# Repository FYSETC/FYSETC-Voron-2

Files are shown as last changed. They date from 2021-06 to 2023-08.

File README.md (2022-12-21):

# FYSETC-VORON-2.4

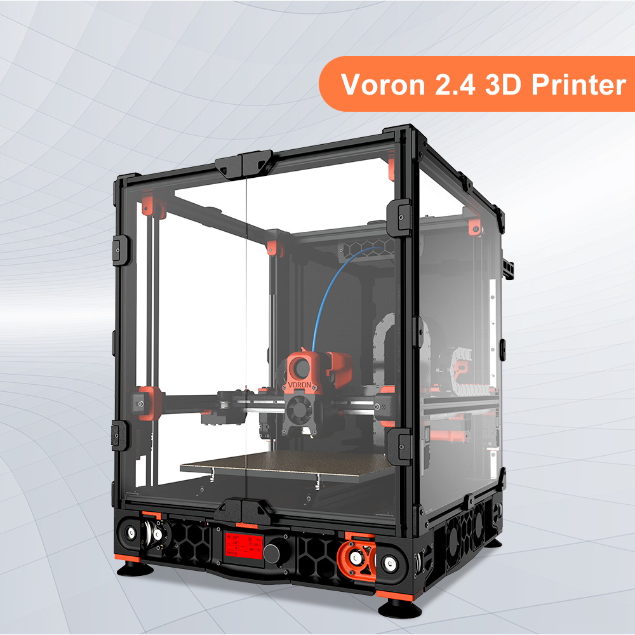
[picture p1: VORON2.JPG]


## 1. Project

This is FYSETC's project database for VORON 2.4 kit, which is convenient for you to find information. Thanks for VORON Team's great work, they always design fantastic printers.

Official website:：https://vorondesign.com/voron2.4
Official Github：https://github.com/VoronDesign/Voron-2/tree/V2.4r2

In folder `Voron-2-Voron2.4` beside this README file, we make some small changes base on the VORON official material. Like change the board to Spider and others. 

## 2. BOM & Changes

Please check BOM [here](https://github.com/FYSETC/FYSETC-Voron-2/blob/main/BOM.md).

### VORON 2.4 R2

## 3. Extra parts

Besides the parts in Voron sourcing guide, we offer extra useful parts for you.

### Wire connector

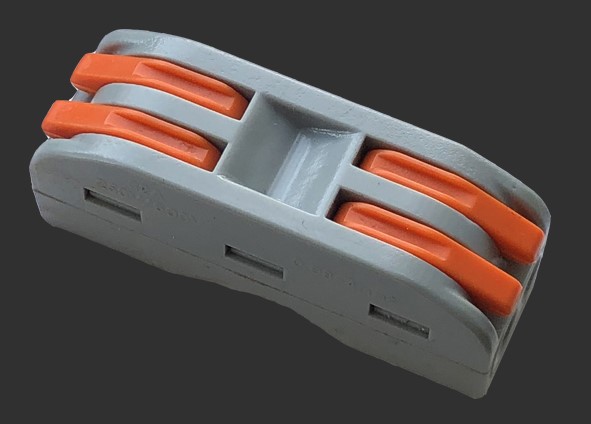
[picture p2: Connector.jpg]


This is for fans wire connection, with this connector you can wire two or more fans to one side of the connector, and the other side  to Spider board. Then you can control the two or more fans with one control pin in Spider.

## 4. Printed parts:

You can find all printed parts in VORON [website](https://vorondesign.com/voron2.4), VORON [github](https://github.com/VoronDesign/Voron-2).

Printed parts are not included in our VORON 2.4 kit. As VORON official provide you options on some particular printed part of the machine. Like the plug panel at the back of VORON machine, you can choose [plug_panel](https://github.com/VoronDesign/Voron-2/blob/Voron2.4/STLs/VORON2.4/Electronics_Compartment/Plug_Panel/plug_panel.stl) or [plug_panel_filtered_mains](https://github.com/VoronDesign/Voron-2/blob/Voron2.4/STLs/VORON2.4/Electronics_Compartment/Plug_Panel/plug_panel_filtered_mains.stl). So in our kit, we also need to choose too, below is our choice.

| Revision 1.0 | Revision 1.1 | Revision 1.2 | Revision 1.3 | R2 |
| --- | --- | --- | --- | --- |
| [plug panel](https://github.com/VoronDesign/Voron-2/blob/Voron2.4/STLs/VORON2.4/Electronics_Compartment/Plug_Panel/plug_panel.stl), [Microswitch edge pod](https://github.com/VoronDesign/VoronUsers/blob/master/printer_mods/randell/Microswitch_Endstop/Microswitch_Edge_Pod.stl), [Z Chain mount part 1](https://github.com/FYSETC/FYSETC-Voron-2/blob/main/Z_Chain_Lower_Mount.STL), [Z Chain mount part 2](https://github.com/FYSETC/FYSETC-Voron-2/blob/main/Z_Chain_Upper_Mount.STL), Spider board mount | [plug panel](https://github.com/VoronDesign/Voron-2/blob/Voron2.4/STLs/VORON2.4/Electronics_Compartment/Plug_Panel/plug_panel.stl), [Microswitch edge pod](https://github.com/VoronDesign/VoronUsers/blob/master/printer_mods/randell/Microswitch_Endstop/Microswitch_Edge_Pod.stl), [Z Chain mount part 1](https://github.com/FYSETC/FYSETC-Voron-2/blob/main/Z_Chain_Lower_Mount.STL), [Z Chain mount part 2](https://github.com/FYSETC/FYSETC-Voron-2/blob/main/Z_Chain_Upper_Mount.STL), Spider board mount | [plug panel](https://github.com/VoronDesign/Voron-2/blob/Voron2.4/STLs/VORON2.4/Electronics_Compartment/Plug_Panel/plug_panel.stl), [Microswitch edge pod](https://github.com/VoronDesign/VoronUsers/blob/master/printer_mods/randell/Microswitch_Endstop/Microswitch_Edge_Pod.stl), [Z Chain mount part](https://github.com/VoronDesign/VoronUsers/tree/master/printer_mods/KiloQubit/VORON_2.4_Z_Chain_3_Hole_Mounts), Spider board mount | [plug panel](https://github.com/VoronDesign/Voron-2/blob/Voron2.4/STLs/VORON2.4/Electronics_Compartment/Plug_Panel/plug_panel.stl), [Microswitch edge pod](https://github.com/VoronDesign/VoronUsers/blob/master/printer_mods/randell/Microswitch_Endstop/Microswitch_Edge_Pod.stl), [Z Chain mount part](https://github.com/VoronDesign/VoronUsers/tree/master/printer_mods/KiloQubit/VORON_2.4_Z_Chain_3_Hole_Mounts), Spider board mount | [Microswitch_Z_Endstop_new_shorter](https://github.com/VoronDesign/Voron-Hardware/tree/master/Microswitch_Z_Endstop/STLs) |

## 5. Wiring

### 5.1 Spider 1.x wiring

There is wiring from VORON community [here](https://github.com/shiftingtech/Voron-Documentation/blob/Spider/build/electrical/v2_spider_wiring.md). Also you can refer Spider wiring [here](https://github.com/FYSETC/FYSETC-SPIDER#3-hardware-guide).

***Note: Check your fan voltage before you set the fan jumpers, the jumpers for fan in below diagram are all set to 24v.***

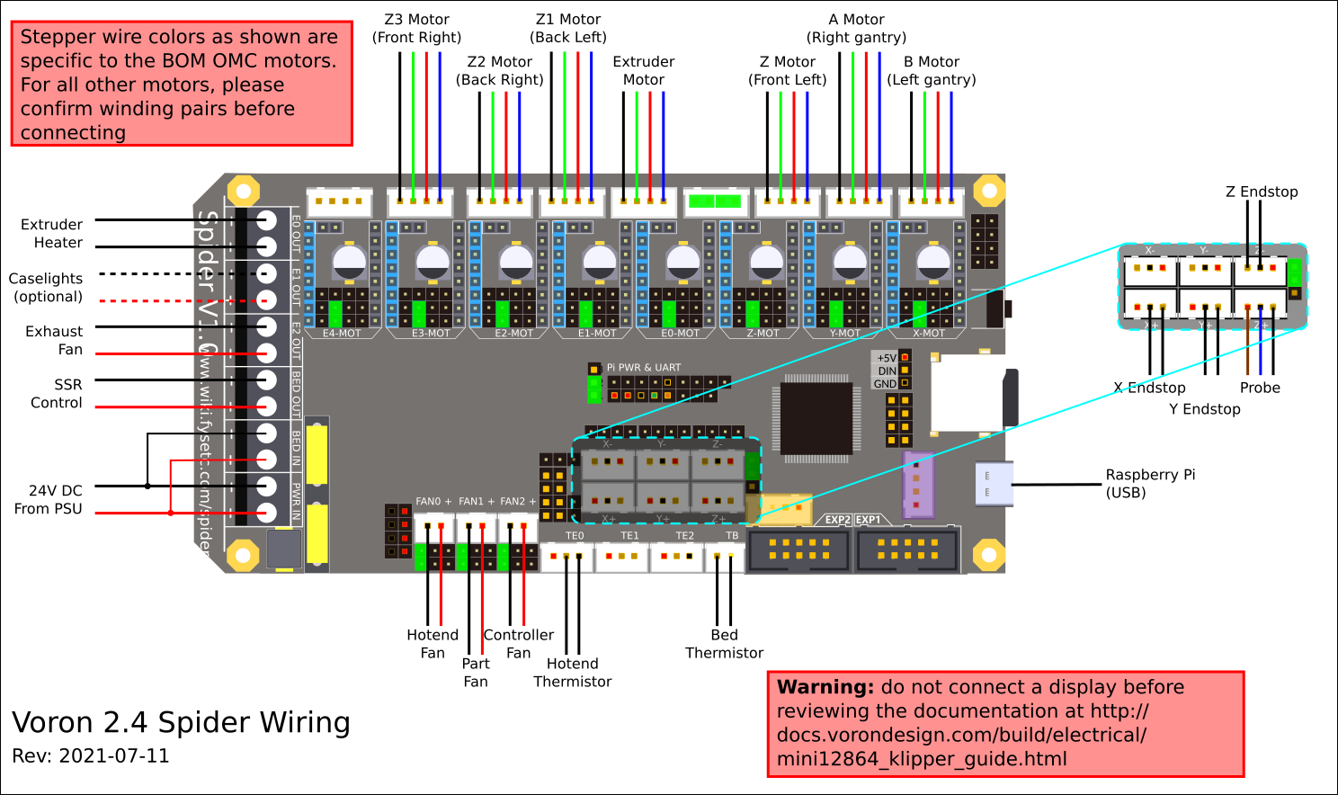
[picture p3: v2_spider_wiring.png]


### 5.2 Spider v2.2 wiring

#### 5.2.1 VORON 2.4 kit wiring

If the pic is not clear enough, please check PDF file [here](https://github.com/FYSETC/FYSETC-Voron-2/blob/main/VORON2.4_SPIDER_V22_WIRING.pdf).



#### 5.2.2 VORON 2.4 R2 kit wiring

##### Spider 2.2

If the pic is not clear enough, please check PDF file [here](https://github.com/FYSETC/FYSETC-Voron-2/blob/main/VORON2.4R2_SPIDER_V22_Wiring_S.pdf).

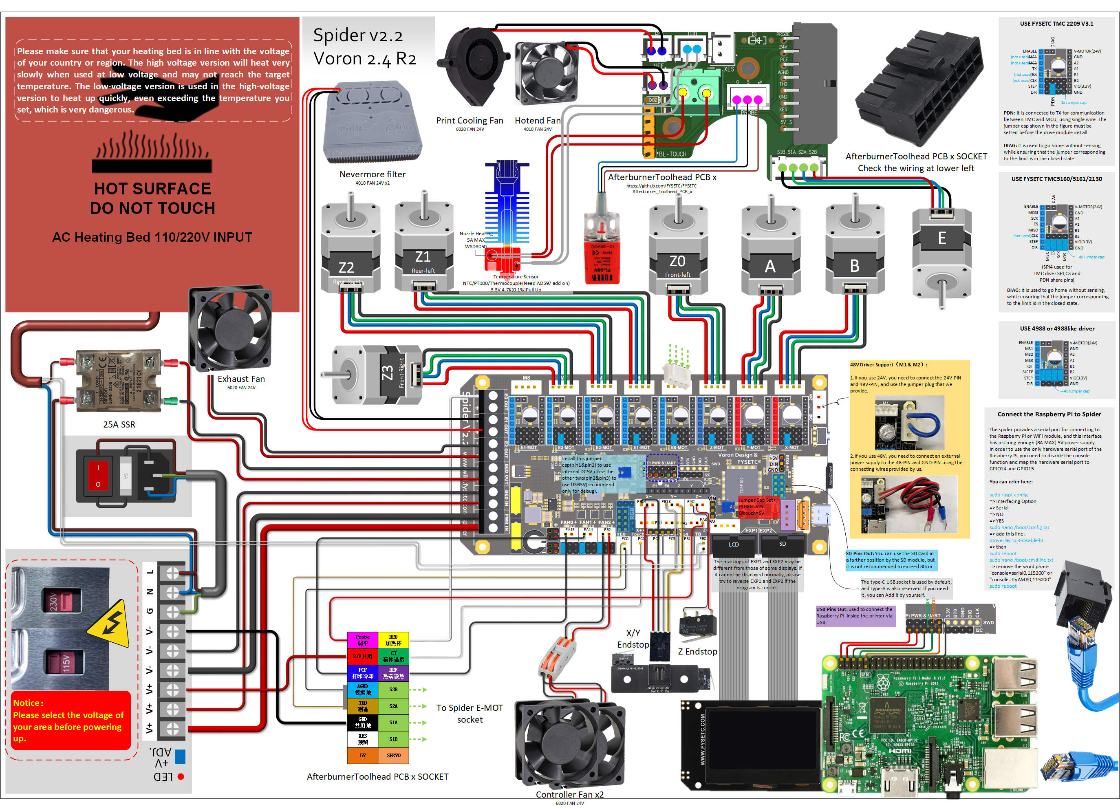
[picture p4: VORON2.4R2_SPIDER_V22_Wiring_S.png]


If the pic is not clear enough, please check PDF type [here](https://github.com/FYSETC/FYSETC-Voron-2/blob/main/VORON2.4R2_SPIDER_V22_Wiring.pdf).

##### Spider 2.3

If the pic is not clear enough, please check PDF file [here](https://github.com/FYSETC/FYSETC-Voron-2/blob/main/VORON2.4R2_SPIDER_V23_Wiring_S.pdf).

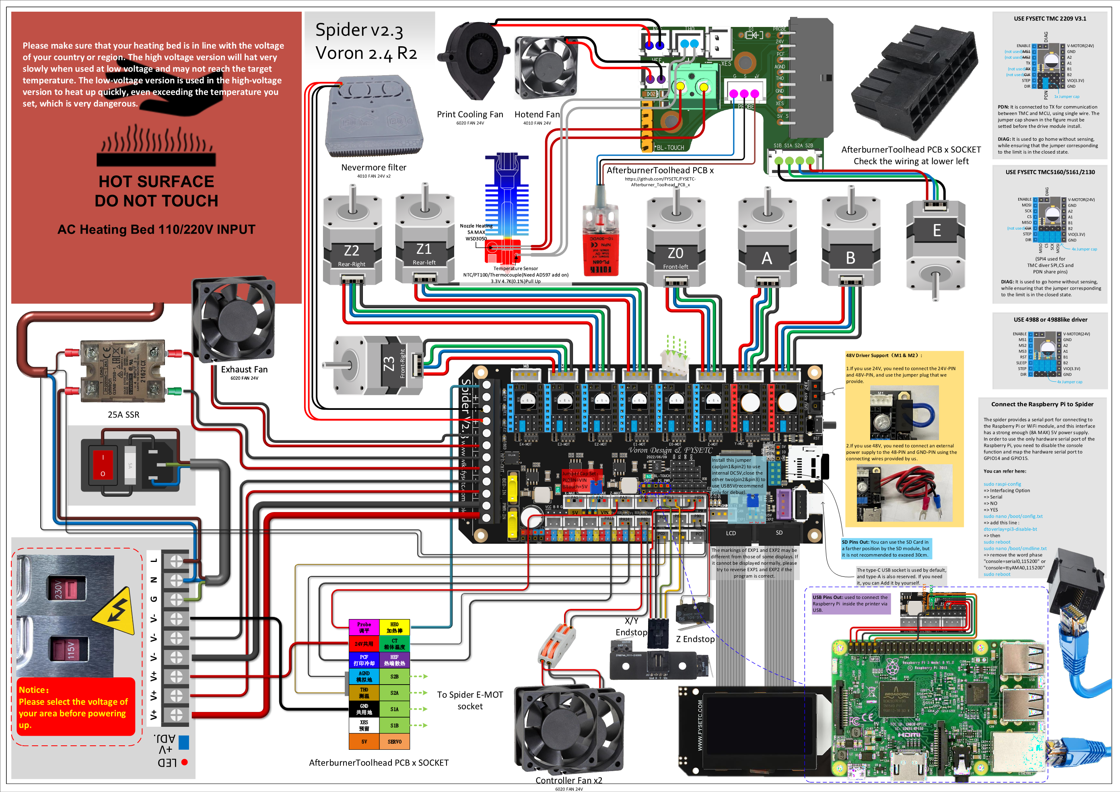
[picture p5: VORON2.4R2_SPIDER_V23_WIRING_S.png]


If the pic is not clear enough, please check PDF type [here](https://github.com/FYSETC/FYSETC-Voron-2/blob/main/VORON2.4R2_SPIDER_V23_Wiring.pdf).



### 5.3 XY endstop

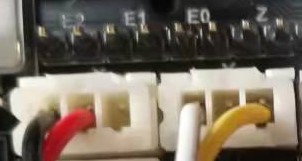
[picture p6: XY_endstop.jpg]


## 6. Firmware&OS

You can find example Klipper printer.cfg file on VORON github [here](https://github.com/VoronDesign/Voron-2/tree/Voron2.4/firmware/klipper_configurations/Spider) or our Spider github [here](https://github.com/FYSETC/FYSETC-SPIDER/blob/main/firmware/Klipper/printer.cfg) or gitee [here](https://gitee.com/fysetc-mirrors/FYSETC-SPIDER/tree/main/firmware/Klipper). And you can get our pre-build firmware and OS image in the `firmware&OS` folder next to this `README` file. 

## 7. Where to buy the kit

[Aliexpress](https://www.aliexpress.com/item/1005002782065110.html)

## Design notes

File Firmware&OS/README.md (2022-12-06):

# Firmware&OS

## 1. Firmware

There is pre-build firmware named `firmware.bin`, please flash it to Spider board flash address `0x08008000`. You can follow Spider firmware upload instruction here ([github](https://github.com/FYSETC/FYSETC-SPIDER#44--firmware-upload) [gitee](https://github.com/FYSETC/FYSETC-SPIDER#44--firmware-upload)).

And the menuconfig of this pre-build firmware is below.

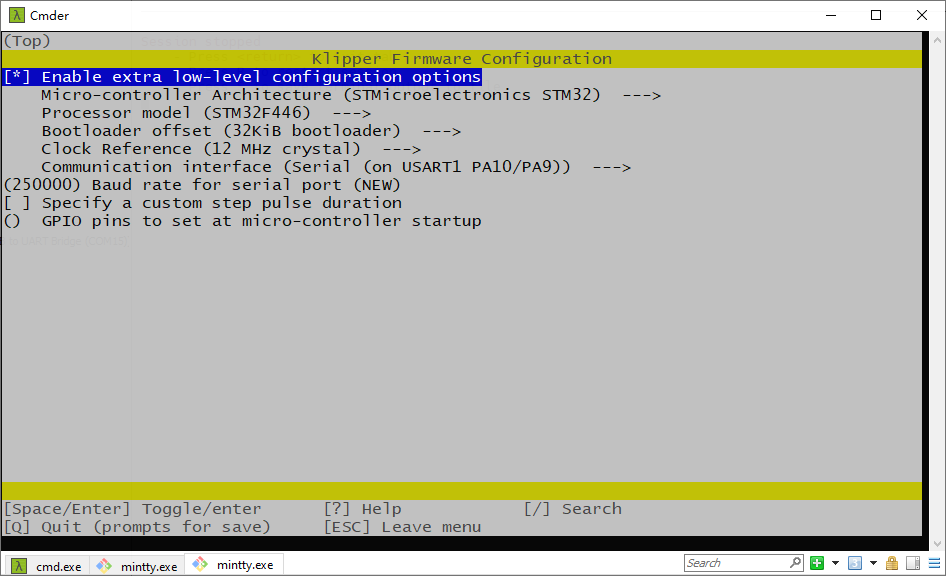
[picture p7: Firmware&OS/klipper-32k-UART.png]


## 2. OS

We provide you two OS images choices: Mainsail OS and Octopi OS.

### 2.1 Mainsail OS

You can get the corresponding Mainsail OS here ([1.Dropbox](https://www.dropbox.com/s/y8eb1giik5p6n1d/VORON2.4R2-Spider2.x-Mainsail.zip?dl=0)).

### 2.2 Octopi OS

If your kit version is rev1.0 or rev1.1, your Spider board version is 1.x, you can get the responding Octopi system here([1.Dropbox](https://www.dropbox.com/s/vtbbxu55y27kbl7/VORON2.4-Octoprint-Klipper.img?dl=0) [2.百度云盘](https://pan.baidu.com/s/1aeOkN2ZxQb99EaApOWNglw) 提取码：1357) . If your kit version is rev1.2, then your Spider board version is 2.2, and you can get the responding Octopi system here([1.Dropbox](https://www.dropbox.com/s/mn1kvcndi1gpb9v/VORON2.4-Spider2.x-Octoprint-Klipper.img?dl=0) [2.百度云盘](https://pan.baidu.com/s/1OZLoSdPNHbxYGWpk1KwKzA) 提取码：YYDS).

You can login in Octoprint with the following account and password.

```
Account: FYSETC
Password: 12345678
```

### 2.3 How to flash OS image

Before flash, you need an SD card , minimum requirement of SD card capacity is 8G. Please prepare that first. And then you can use this software [here](https://www.balena.io/etcher/) to install. Well that are so many OS flash tool that you can use. And there are a lot of tutorial if you google `how to flash os image`.

### 2.4 SSH account and password

OS SSH account and password

```
Account: pi
Password: raspberry
```

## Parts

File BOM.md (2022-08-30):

# Package list 

## Revision 1.0

| Index | Sort | Component | Qty | Note |
| ----- | --- | --- | --- | --- |
| 1 | Fasteners | Voron V2.4 fasteners Pack | 1 SET | |
| 2 | Motion | GT2 Open Belt LL-2GT-6 (6mm wide) - 4000mm | 1 PC | |
| 3 | Motion | GT2 Open Belt LL-2GT-9 (9mm wide) - 4440mm | 1 PC | |
| 4 | Motion | GT2 Belt Loop (6mm W) - 188mm | 4 PCS | |
| 5 | Motion | GT2 20T Pulley (5mm ID 6mm W) | 3 PCS | |
| 6 | Motion | GT2 16T Pulley (5mm ID 6mm W) | 4 PCS | |
| 7 | Motion | GT2 20T Pulley (5mm ID 9mm W) | 4 PCS | |
| 8 | Motion | GT2 20T Toothed Idler (5mm ID 6mm W) | 2 PCS | |
| 9 | Motion | GT2 20T Toothed Idler (5mm ID 9mm W) | 4 PCS | |
| 10 | Motion | GT2 80T Pulley (5mm ID 6mm W) | 4 PCS | |
| 11 | Motion | F695 Bearing | 20 PCS | |
| 12 | Motion | 625 Bearing | 12 PCS | |
| 13 | Motion | 5x60mm Shaft | 4 PCS | |
| 14 | Motion | 5x30mm Shaft | 1 PC | |
| 15 | Motion | Linear Rail MGN9H 400mm | 8 PCS | |
| 16 | Vibration Management | Rubber Compressor Foot | 4 PCS | |
| 17 | Electronics | XY Microswitch Endstop / Z Endstop | 1 PC / 1 SET | [Here](https://github.com/VoronDesign/Voron-Hardware/tree/master/Microswitch_Endstop) |
| 18 | Electronics | PL-08N Inductive Probe | 1 PC | |
| 19 | Electronics | SSR: G3A-210B-DC5 | 1 PC | |
| 20 | Electronics | NEMA17 Motor TB-3544(check [here](https://github.com/FYSETC/FYSETC-MOTORS/tree/main/TB-3544)) | 6 PCS | 5x1m cables for Z0 Z1 Z2 Z3 and B motor, 1x1.4m for A motor  |
| 21 | Electronics | NEMA17 Motor MSM-30010-R0005(check [here](https://github.com/FYSETC/FYSETC-MOTORS/tree/main/MSM-30010-R0005)) | 1 PC | 1x2.3m for E motor |
| 22 | Electronics | Mean Well LRS-200-24 PSU | 1 PC | |
| 23 | Electronics | Inlet Power Socket IEC320 C14 | 1 SET | |
| 24 | Electronics | 40x40x10 Axial Fan (24V) | 1 PCS | |
| 25 | Electronics | 40x40x20 Centrifugal Fan (24V) | 1 PC | |
| 26 | Electronics | 60x60x20 Fan (24V)kit | 1 SET | |
| 27 | Electronics | Keystone CAT6 Insert (Optional) | 1 PC | |
| 28 | Electronics | C13 Power Cord | 1 PC | |
| 29 | Controller | RaspberryPi | 1 PC | |
| 30 | Controller | USB C power cable | 1 PC | |
| 31 | Controller | Spider Board | 1 PC | |
| 32 | Controller | TMC2209 Stepper Motor Driver | 7 PCS | |
| 33 | Controller | Mini 12864 Display | 1 PC | cable length 300mm |
| 34 | Frame | OpenBuilds Angle Corner Connector | 4 PCS | |
| 35 | Frame | Misumi sectional profile Kit HFSB5-2020 SET | 18 PCS | |
| 36 | Misc | PTFE Tube (4mm OD 2mm ID) - 300mm | 1 PC | |
| 37 | Misc | PTFE Tube (4mm OD 3mm ID) - 1m | 1 PC | |
| 38 | Misc | 46.6x3mm Neodimium Magnet | 8 PCS | |
| 39 | Misc | 4mm Bowden Coupler | 1 PC | |
| 40 | Misc | BMG Extruder Componnets Kit | 1 SET | |
| 41 | Misc | E3D V6 Bowden Hotend Kit (24V) | 1 SET | |
| 42 | Misc | DIN 3 Rails (35mm W) - 460mm | 2 PCS | |
| 43 | Misc | DIN Rail Mount Bracket for G3A SSR | 1 PC | |
| 44 | Misc | Fume Extractor Carbon Filter Element | 1 PC | |
| 45 | Misc | 3M VHB Tape 5952 | 1 PC | |
| 46 | Misc | Tesa Wire Loom Harness Tape | 1 PC | |
| 47 | Cables | Cable Kit | 1 SET | |
| 48 | Cables | E2-10-10-018-0 Chain (405mm [1.33ft]) | 3 PCS | |
| 49 | Panels | Bottom/Back/Electronics Bay Panels | 3 PCS | |
| 50 | Panels | Side/Front/Top Acrylic Panels | 4 PCS | |
| 51 | Buildplate | MIC6 5/16" Plate - 14"x14" | 1 PC | |
| 52 | Buildplate | Silicone AC Heater - 300x300mm (650W) | 1 PC | Thermal Fuse RH15A125 wired |
| 53 | Buildplate | Textured steel plate 355*355mm | 1 PC | |
| 54 | Buildplate | Magnetic stickers 355*355mm | 1 PC | |
## Revision 1.1

| Index | Sort | Component | Qty | Note |
| ----- | --- | --- | --- | --- |
| 1 | Fasteners | Voron V2.4 fasteners Pack | 1 SET | v1.1 add more fasterners |
| 2 | Motion | GT2 Open Belt LL-2GT-6 (6mm wide) - 4000mm | 1 PC | v1.2 add more length |
| 3 | Motion | GT2 Open Belt LL-2GT-9 (9mm wide) - 4440mm | 1 PC | v1.2 add more length |
| 4 | Motion | GT2 Belt Loop (6mm W) - 188mm | 4 PCS | |
| 5 | Motion | GT2 20T Pulley (5mm ID 6mm W) | 3 PCS | |
| 6 | Motion | GT2 16T Pulley (5mm ID 6mm W) | 4 PCS | |
| 7 | Motion | GT2 20T Pulley (5mm ID 9mm W) | 4 PCS | |
| 8 | Motion | GT2 20T Toothed Idler (5mm ID 6mm W) | 2 PCS | |
| 9 | Motion | GT2 20T Toothed Idler (5mm ID 9mm W) | 4 PCS | |
| 10 | Motion | GT2 80T Pulley (5mm ID 6mm W) | 4 PCS | |
| 11 | Motion | F695 Bearing | 20 PCS | |
| 12 | Motion | 625 Bearing | 12 PCS | |
| 13 | Motion | 5x60mm Shaft | 4 PCS | |
| 14 | Motion | 5x30mm Shaft | 1 PC | |
| 15 | Motion | Linear Rail MGN9H 400mm | 8 PCS | |
| 16 | Vibration Management | Rubber Compressor Foot | 4 PCS | |
| 17 | Electronics | XY Microswitch Endstop / Z Endstop | 1 PC / 1 SET | [Here](https://github.com/VoronDesign/Voron-Hardware/tree/master/Microswitch_Endstop) |
| 18 | Electronics | PL-08N Inductive Probe | 1 PC | |
| 19 | Electronics | SSR: G3A-210B-DC5 | 1 PC | |
| 20 | Electronics | NEMA17 Motor TB-3544(check [here](https://github.com/FYSETC/FYSETC-MOTORS/tree/main/TB-3544)) | 6 PCS | 5x1m cables for Z0 Z1 Z2 Z3 and B motor, 1x1.4m for A motor  |
| 21 | Electronics | NEMA17 Motor MSM-30010-R0005(check [here](https://github.com/FYSETC/FYSETC-MOTORS/tree/main/MSM-30010-R0005)) | 1 PC | 1x2.3m for E motor |
| 22 | Electronics | Mean Well LRS-200-24 PSU | 1 PC | |
| 23 | Electronics | Inlet Power Socket IEC320 C14 | 1 SET | |
| 24 | Electronics | 40x40x10 Axial Fan (24V) | 1 PCS | |
| 25 | Electronics | 40x40x20 Centrifugal Fan (24V) | 1 PC | |
| 26 | Electronics | 60x60x20 Fan (24V)kit | 1 SET | |
| 27 | Electronics | Keystone CAT6 Insert (Optional) | 1 PC | |
| 28 | Electronics | C13 Power Cord | 1 PC | |
| 29 | Controller | RaspberryPi | 1 PC | |
| 30 | Controller | USB C power cable | 1 PC | v1.1 change to USB data cable |
| 31 | Controller | Spider Board | 1 PC | |
| 32 | Controller | TMC2209 Stepper Motor Driver | 7 PCS | |
| 33 | Controller | Mini 12864 Display | 1 PC | v1.1 cable length 400mm |
| 34 | Frame | OpenBuilds Angle Corner Connector | 4 PCS | |
| 35 | Frame | Misumi sectional profile Kit HFSB5-2020 SET | 18 PCS | |
| 36 | Misc | PTFE Tube (4mm OD 2mm ID) - 300mm | 1 PC | |
| 37 | Misc | PTFE Tube (4mm OD 3mm ID) - 1m | 1 PC | |
| 38 | Misc | 46.6x3mm Neodimium Magnet | 8 PCS | |
| 39 | Misc | 4mm Bowden Coupler | 1 PC | |
| 40 | Misc | BMG Extruder Componnets Kit | 1 SET | |
| 41 | Misc | E3D V6 Bowden Hotend Kit (24V) | 1 SET | |
| 42 | Misc | DIN 3 Rails (35mm W) - 460mm | 2 PCS | |
| 43 | Misc | DIN Rail Mount Bracket for G3A SSR | 1 PC | |
| 44 | Misc | Fume Extractor Carbon Filter Element | 1 PC | |
| 45 | Misc | 3M VHB Tape 5952 | 1 PC | |
| 46 | Misc | Tesa Wire Loom Harness Tape | 1 PC | |
| 47 | Cables | Cable Kit | 1 SET | |
| 48 | Cables | E2-10-10-018-0 Chain (405mm [1.33ft]) | 3 PCS | |
| 49 | Panels | Bottom/Back/Electronics Bay Panels | 3 PCS | |
| 50 | Panels | Side/Front/Top Acrylic Panels | 4 PCS | |
| 51 | Buildplate | MIC6 5/16" Plate - 14"x14" | 1 PC | |
| 52 | Buildplate | Silicone AC Heater - 300x300mm (650W) | 1 PC | Thermal Fuse RH15A125 wired |
| 53 | Buildplate | Textured steel plate 355*355mm | 1 PC | |
| 54 | Buildplate | Magnetic stickers 355*355mm | 1 PC | |

## Revision 1.2

| Index | Sort | Component | Qty | Note |
| ----- | --- | --- | --- | --- |
| 1 | Fasteners | Voron V2.4 fasteners Pack | 1 SET | |
| 2 | Motion | GT2 Open Belt LL-2GT-6 (6mm wide) - 2100mm | 2 PC | |
| 3 | Motion | GT2 Open Belt LL-2GT-9 (9mm wide) - 1200mm | 4 PC | |
| 4 | Motion | GT2 Belt Loop (6mm W) - 188mm | 4 PCS | |
| 5 | Motion | GT2 20T Pulley (5mm ID 6mm W) | 3 PCS | |
| 6 | Motion | GT2 16T Pulley (5mm ID 6mm W) | 4 PCS | |
| 7 | Motion | GT2 20T Pulley (5mm ID 9mm W) | 4 PCS | |
| 8 | Motion | GT2 20T Toothed Idler (5mm ID 6mm W) | 2 PCS | |
| 9 | Motion | GT2 20T Toothed Idler (5mm ID 9mm W) | 4 PCS | |
| 10 | Motion | GT2 80T Pulley (5mm ID 6mm W) | 4 PCS | |
| 11 | Motion | F695 Bearing | 20 PCS | |
| 12 | Motion | 625 Bearing | 12 PCS | |
| 13 | Motion | 5x60mm Shaft | 4 PCS | |
| 14 | Motion | 5x30mm Shaft | 1 PC | |
| 15 | Motion | Linear Rail MGN9H 400mm | 8 PCS | |
| 16 | Vibration Management | Rubber Compressor Foot | 4 PCS | |
| 17 | Electronics | XY Microswitch Endstop / Z Endstop | 1 PC / 1 SET | [Here](https://github.com/VoronDesign/Voron-Hardware/tree/master/Microswitch_Endstop) |
| 18 | Electronics | PL-08N Inductive Probe | 1 PC | |
| 19 | Electronics | SSR: G3A-210B-DC5 | 1 PC | |
| 20 | Electronics | NEMA17 Motor TB-3544(check [here](https://github.com/FYSETC/FYSETC-MOTORS/tree/main/TB-3544)) | 6 PCS | 5x1m cables for Z0 Z1 Z2 Z3 and B motor, 1x1.4m for A motor  |
| 21 | Electronics | NEMA17 Motor MSM-30010-R0005(check [here](https://github.com/FYSETC/FYSETC-MOTORS/tree/main/MSM-30010-R0005)) | 1 PC | 1x2.3m for E motor |
| 22 | Electronics | Mean Well LRS-200-24 PSU | 1 PC | |
| 23 | Electronics | Inlet Power Socket IEC320 C14 | 1 SET | |
| 24 | Electronics | 40x40x10 Axial Fan (24V) | 1 PCS | |
| 25 | Electronics | 40x40x20 Centrifugal Fan (24V) | 1 PC | |
| 26 | Electronics | 60x60x20 Fan (24V)kit | 1 SET | |
| 27 | Electronics | Keystone CAT6 Insert (Optional) | 1 PC | |
| 28 | Electronics | C13 Power Cord | 1 PC | |
| 29 | Controller | RaspberryPi | 1 PC | |
| 30 | Controller | sdcard | 1 PC | v1.2 added |
| 31 | Controller | USB C cable | 1 PC | |
| 32 | Controller | Spider Board | 1 PC | v1.2 Pre-build Klipper flashed |
| 33 | Controller | TMC2209 Stepper Motor Driver | 7 PCS | |
| 34 | Controller | Mini 12864 Display | 1 PC | |
| 35 | Frame | OpenBuilds Angle Corner Connector | 4 PCS | |
| 36 | Frame | Misumi sectional profile Kit HFSB5-2020 SET | 18 PCS | |
| 37 | Misc | PTFE Tube (4mm OD 2mm ID) - 300mm | 1 PC | |
| 38 | Misc | PTFE Tube (4mm OD 3mm ID) - 1m | 1 PC | |
| 39 | Misc | 46.6x3mm Neodimium Magnet | 8 PCS | |
| 40 | Misc | 4mm Bowden Coupler | 1 PC | |
| 41 | Misc | BMG Extruder Componnets Kit | 1 SET | |
| 42 | Misc | E3D V6 Bowden Hotend Kit (24V) | 1 SET | |
| 43 | Misc | DIN 3 Rails (35mm W) - 460mm | 2 PCS | |
| 44 | Misc | DIN Rail Mount Bracket for G3A SSR | 1 PC | |
| 45 | Misc | Fume Extractor Carbon Filter Element | 1 PC | |
| 46 | Misc | 3M VHB Tape 5952 | 1 PC | |
| 47 | Misc | Tesa Wire Loom Harness Tape | 1 PC | |
| 48 | Misc | XH2.54 2/3/4 Pin Plastic shell | 1 SET | v1.2 added |
| 49 | Mics | Zipties | 1 SET | v1.2 added |
| 50 | Cables | Cable Kit | 1 SET | |
| 51 | Cables | E2-10-10-018-0 Chain (405mm [1.33ft]) | 3 PCS | |
| 52 | Panels | Bottom/Back/Electronics Bay Panels | 3 PCS | |
| 53 | Panels | Side/Front/Top Acrylic Panels | 4 PCS | |
| 54 | Buildplate | MIC6 5/16" Plate - 14"x14" | 1 PC | |
| 55 | Buildplate | Silicone AC Heater - 300x300mm (650W) | 1 PC | Thermal Fuse RH15A125 wired |
| 56 | Buildplate | Textured steel plate 355*355mm | 1 PC | |
| 57 | Buildplate | Magnetic stickers 355*355mm | 1 PC | |
| 58 | Tool | Cutting pliers | 1 PC | v1.2 added |
| 59 | Tool | Hexagonal wrenchs | 1 SET | v1.2 added |
| 60 | Tool | Thermal silica | 1 PC | v1.2 added |

## Revision 1.3

| Index | Sort | Component | Qty | Note |
| ----- | --- | --- | --- | --- |
| 1 | Fasteners | Voron V2.4 fasteners Pack | 1 SET | |
| 2 | Motion | GT2 Open Belt LL-2GT-6 (6mm wide) - 2100mm | 2 PC | |
| 3 | Motion | GT2 Open Belt LL-2GT-9 (9mm wide) - 1200mm | 4 PC | |
| 4 | Motion | GT2 Belt Loop (6mm W) - 188mm | 4 PCS | |
| 5 | Motion | GT2 20T Pulley (5mm ID 6mm W) | 3 PCS | v1.2 1PC remove end cap |
| 6 | Motion | GT2 16T Pulley (5mm ID 6mm W) | 4 PCS | |
| 7 | Motion | GT2 20T Pulley (5mm ID 9mm W) | 4 PCS | |
| 8 | Motion | GT2 20T Toothed Idler (5mm ID 6mm W) | 2 PCS | |
| 9 | Motion | GT2 20T Toothed Idler (5mm ID 9mm W) | 4 PCS | |
| 10 | Motion | GT2 80T Pulley (5mm ID 6mm W) | 4 PCS | |
| 11 | Motion | F695 Bearing | 20 PCS | |
| 12 | Motion | 625 Bearing | 12 PCS | |
| 13 | Motion | 5x60mm Shaft | 4 PCS | |
| 14 | Motion | 5x30mm Shaft | 1 PC | |
| 15 | Motion | Linear Rail MGN9H 400mm | 8 PCS | |
| 16 | Vibration Management | Rubber Compressor Foot | 4 PCS | |
| 17 | Electronics | XY Microswitch Endstop / Z Endstop | 1 PC / 1 SET | [Here](https://github.com/VoronDesign/Voron-Hardware/tree/master/Microswitch_Endstop) |
| 18 | Electronics | PL-08N Inductive Probe | 1 PC | |
| 19 | Electronics | Omron G3NB-225B-1 SSR | 1 PC | v1.2 Change to Omron |
| 20 | Electronics | NEMA17 Motor  17HS19-2004S-C (check [here](https://github.com/FYSETC/FYSETC-MOTORS/tree/main/17HS19-2004S-C)) | 6 PCS | v1.2 5x1.3m cables for Z0 Z1 Z2 Z3 and B motor, 1x1.7m for A motor |
| 21 | Electronics | NEMA17 Motor 42HS20401B-20-2.6M(check [here](https://github.com/FYSETC/FYSETC-MOTORS/tree/main/42HS20401B-20-2.6M)) | 1 PC | v1.2 1x2.6m for E motor |
| 22 | Electronics | Mean Well LRS-200-24 PSU | 1 PC | |
| 23 | Electronics | Inlet Power Socket IEC320 C14 | 1 SET | |
| 24 | Electronics | 40x40x10 Axial Fan (24V) | 1 PCS | v1.2 Change the cable length to 2.6 m |
| 25 | Electronics | 40x40x20 Centrifugal Fan (24V) | 1 PC | v1.2 Change the cable length to 2.6 m |
| 26 | Electronics | 60x60x20 Fan (24V)kit | 1 SET | v1.2 1PC change the cable length to 1.2 m，2PCS change the cable length to 0.4 m |
| 27 | Electronics | Keystone CAT6 Insert (Optional) | 1 PC | |
| 28 | Electronics | C13 Power Cord | 1 PC | |
| 29 | Controller | RaspberryPi | 1 PC | |
| 30 | Controller | sdcard | 1 PC | |
| 31 | Controller | USB C cable | 1 PC | |
| 32 | Controller | Spider Board | 1 PC | |
| 33 | Controller | TMC2209 Stepper Motor Driver | 7 PCS | |
| 34 | Controller | Mini 12864 Display | 1 PC | |
| 35 | Frame | OpenBuilds Angle Corner Connector | 4 PCS | |
| 36 | Frame | Misumi sectional profile Kit HFSB5-2020 SET | 18 PCS | |
| 37 | Misc | PTFE Tube (4mm OD 2mm ID) - 300mm | 1 PC | |
| 38 | Misc | PTFE Tube (4mm OD 3mm ID) - 1m | 1 PC | |
| 39 | Misc | 6x3mm Neodimium Magnet | 10 PCS | v1.2 2 more pcs added |
| 40 | Misc | 4mm Bowden Coupler | 1 PC | |
| 41 | Misc | BMG Extruder Componnets Kit | 1 SET | |
| 42 | Misc | E3D V6 Bowden Hotend Kit (24V) | 1 SET | v1.2 Contains Titanium Alloy Bi-Metal Heatbreak+High quality heat block |
| 43 | Misc | DIN 3 Rails (35mm W) - 460mm | 2 PCS | |
| 44 | Misc | DIN Rail Mount Bracket for G3A SSR | 1 PC | |
| 45 | Misc | Fume Extractor Carbon Filter Element | 1 PC | |
| 46 | Misc | 3M VHB Tape 5952 | 1 PC | v1.2 Change to 2.0cm |
| 47 | Misc | Foam Tape Thickness 1mm Length 5m | 3PCS | v1.2 added |
| 48 | Misc | Tesa Wire Loom Harness Tape | 1 PC | |
| 49 | Misc | XH2.54 2/3/4 Pin Plastic shell | 1 SET | |
| 50 | Mics | Zipties | 1 SET | |
| 51 | Cables | Cable Kit | 1 SET | v1.2 Pre-crimped terminals and longer wire lengths |
| 52 | Cables | VORON 2.4 Chain Kit (1PC 15X10mm，2PCS 10X11) | 1 SET | v1.2 prewired according to axis length |
| 53 | Panels | Bottom/Back/Electronics Bay Panels | 3 PCS | |
| 54 | Panels | Side/Front/Top Acrylic Panels | 4 PCS | |
| 55 | Buildplate | MIC6 5/16" Plate - 14"x14" | 1 PC | |
| 56 | Buildplate | Silicone AC Heater - 300x300mm (650W) | 1 PC | Thermal Fuse RH15A125 wired |
| 57 | Buildplate | Thermal Fuse RH15A125 | 1 PC | v1.2 added |
| 58 | Buildplate | JanusBPS Textured steel plate 355*355mm （One side pattern and the other side glossy PEI sticker） | 1 PC | v1.2 changed to [JanusBPS](https://www.google.com/search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) |
| 59 | Buildplate | Magnetic stickers 355*355mm | 1 PC | |
| 60 | Tool | Cutting pliers | 1 PC | |
| 61 | Tool | Hexagonal wrenchs | 1 SET | |
| 62 | Tool | Thermal silica | 1 PC | |
| 63 | Misc | Klicky-Probe kit | 1 SET | |
## VORON 2.4 R2 Revision 1.0

| Index | Sort | Component | Qty | Note |
| ----- | --- | --- | --- | --- |
| 1 | Fasteners | Voron V2.4 R2 fasteners Pack | 1 SET | |
| 2 | Motion | GATES GT2 Open Belt LL-2GT-6 (6mm wide) - 1800/2000mm | 2 PC | |
| 3 | Motion | GATES GT2 Open Belt LL-2GT-9 (9mm wide) - 1100/1200mm | 4 PC | |
| 4 | Motion | GATES GT2 Belt Loop (6mm W) - 188mm | 4 PCS | |
| 5 | Motion | GT2 20T Pulley (5mm ID 6mm W) 1PC remove end cap | 3 PCS | |
| 6 | Motion | GT2 16T Pulley (5mm ID 6mm W) | 4 PCS | |
| 7 | Motion | GT2 20T Pulley (5mm ID 9mm W) | 4 PCS | |
| 8 | Motion | GT2 20T Toothed Idler (5mm ID 6mm W) | 2 PCS | |
| 9 | Motion | GT2 20T Toothed Idler (5mm ID 9mm W) | 4 PCS | |
| 10 | Motion | GT2 80T Pulley (5mm ID 6mm W) | 4 PCS | |
| 11 | Motion | F695 Bearing | 20 PCS | |
| 12 | Motion | 625 Bearing | 12 PCS | |
| 13 | Motion | 5x60mm Shaft | 4 PCS | |
| 14 | Motion | 5x29.5mm Shaft | 1 PC | |
| 15 | Motion | Linear Rail MGN9H 350/400mm | 6 PCS | |
| 16 | Motion | Linear Rail MGN12H 350/400mm | 1 PCS | |
| 17 | Vibration Management | Rubber Compressor Foot | 4 PCS | |
| 18 | Electronics | Afterburner_Toolhead_X_PCB | 1 PC | |
| 19 | Electronics | Afterburner_Toolhead_X_PCB Teflon wiring | 1 PC | |
| 20 | Electronics | XY Microswitch Endstop / Z Endstop | 1 PC / 1 SET | [Here](https://github.com/VoronDesign/Voron-Hardware/tree/master/Microswitch_Z_Endstop) |
| 21 | Electronics | Omron TL-Q5MC2 - NPN Inductive Probe | 1 PC | |
| 22 | Electronics | Omron G3NB-225B-1 SSR | 1 PC | |
| 23 | Electronics | NEMA17 Motor  17HS19-2004S-C (check [here](https://github.com/FYSETC/FYSETC-MOTORS/tree/main/17HS19-2004S-C)) | 6 PCS | |
| 24 | Electronics | NEMA17 Motor 42HS20401B-20-0.05M(check [here](https://github.com/FYSETC/FYSETC-MOTORS/tree/main/42HS20401B-20-2.6M)) | 1 PC | |
| 25 | Electronics | Mean Well LRS-200-24 PSU | 1 PC | |
| 26 | Electronics | Inlet Power Socket IEC320 C14 | 1 SET | |
| 27 | Electronics | 40x40x10 Axial Fan (24V) | 1 PC | |
| 28 | Electronics | 40x40x20 Centrifugal Fan (24V) | 1 PC | |
| 29 | Electronics | 60x60x20 Fan (24V)kit（3 PCS） | 1 SET | |
| 30 | Electronics | Keystone CAT6 Insert (Optional) | 1 PC | |
| 31 | Electronics | C13 Power Cord | 1 PC | |
| 32 | Controller | RaspberryPi（Optional） | 1 PC | |
| 33 | Controller | sdcard 16GB | 1 PC | |
| 34 | Controller | USB C cable | 1 PC | |
| 35 | Controller | Spider Board | 1 PC | |
| 36 | Controller | TMC2209 Stepper Motor Driver | 7 PCS | |
| 37 | Controller | Mini 12864 Display | 1 PC | |
| 38 | Frame | OpenBuilds Angle Corner Connector | 4 PCS | |
| 39 | Frame | Misumi sectional profile Kit HFSB5-2020 SET | 18 PCS | |
| 40 | Misc | PTFE Tube (4mm OD 2mm ID) - 1.5m | 1 PC | |
| 41 | Misc | 6x3mm Neodimium Magnet | 10 PCS | |
| 42 | Misc | 4mm Bowden Coupler | 1 PC | |
| 43 | Misc | BMG Extruder Componnets Kit | 1 SET | |
| 44 | Misc | E3D V6 Bowden Hotend Kit (24V) Titanium Alloy Bi-Metal Heatbreak | 1 SET | |
| 45 | Misc | Heater φ6X15 24V 50W | 1 PC | |
| 46 | Misc | Thermistor NTC 100K B3950 | 1 PC | |
| 47 | Misc | DIN 3 Rails (35mm W) - 460mm | 2 PCS | |
| 48 | Misc | DIN Rail Mount Bracket for G3A SSR | 1 PC | |
| 49 | Misc | Fume Extractor Carbon Filter Element | 1 PC | |
| 50 | Misc | 3M VHB Tape 5952 | 1 PC | |
| 51 | Misc | Foam Tape Thickness 1mm Length 5m | 1PC | |
| 52 | Misc | Foam Tape Thickness 3mm Length 4m | 2 PCS | |
| 53 | Misc | XH2.54 2/3/4 Pin Plastic shell | 1 SET | |
| 54 | Mics | Zipties | 1 SET | |
| 55 | Cables | Cable Kit（Pre-crimped terminals and longer wire lengths with label） | 1 SET | |
| 56 | Cables | VORON 2.4 Chain Kit (1PC 15X10mm，2PCS 10X11) | 1 SET | |
| 57 | Panels | Bottom/Back/Electronics Bay Panels | 3 PCS | |
| 58 | Panels | Side/Front/Top Acrylic Panels | 4 PCS | |
| 59 | Buildplate | MIC6 5/16" Plate - 305X305/355X355mm | 1 PC | |
| 60 | Buildplate | Silicone AC Heater - 250X250/300x300mm (600/750W)+Thermal Fuse RH15A125（Pluggable） | 1 PC | |
| 61 | Buildplate | JanusBPS Textured steel plate 305X305/355X355mm （One side pattern and the other side glossy PEI sticker） | 1 PC | [JanusBPS](https://www.google.com/search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) |
| 62 | Buildplate | Magnetic stickers 305X305/355X355mm thickness 2mm | 1 PC | |
| 63 | Buildplate | Insulation cotton thickness 5mm | 1 PC | |
| 64 | Tool | Cutting pliers | 1 PC | |
| 65 | Tool | Hexagonal wrenchs | 1 SET | |
| 66 | Tool | Thermal silica | 1 PC | |
| 67 | Mics | PVC wiring duct 30x30mm | 1 SET | |
| 68 | Mics | Wago 221-415 Terminals | 3 PCS | |
| 69 | Mics | VORON Nevermore V5 | 1 SET | |
| 70 | Mics | Weaving casing | 1 SET | |
| 71 | Mics | The standby line 3m | 1 PC | |
| 72 | Mics | Wiring diagram | 1 PC | |
| 73 | Electronics | Klicky-Probe kit | 1 SET | |

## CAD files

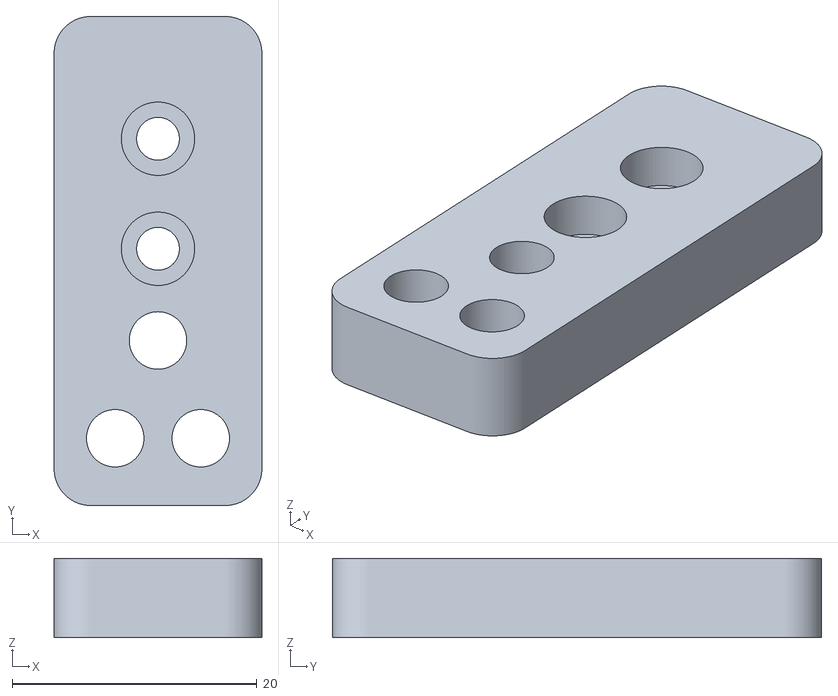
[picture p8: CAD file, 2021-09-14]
Z_Chain_Upper_Mount.STL
17.0 x 40.0 x 6.50

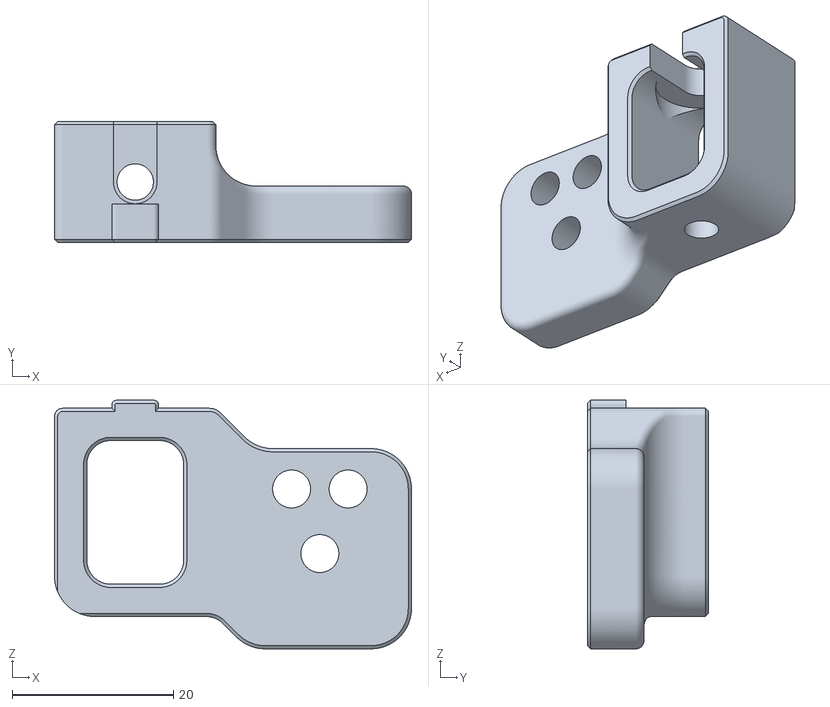
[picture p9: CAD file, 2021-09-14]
Z_Chain_Lower_Mount.STL
44.2 x 15.0 x 30.8

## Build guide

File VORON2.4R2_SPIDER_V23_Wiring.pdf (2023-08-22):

L1

L3

L1

N1

PE1

GND

Bed L

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
Exhaust Fan(EF)

Heater E(HE0)

Z0

Z2

Z1

Zmin Ymin Xmin
HotendFan(HEF)

PrintFan(PCF)

ControllerFan(CF)

TB

EXP1 | EXP2
EXP1 | EXP2

PROBE

ControllerFan(CF)

Relay
Signal
(RS)

Relay Signal(RS)

### FYSETC Voron 2.4 kit Wring example- by George Fu

Docs
Find kit details(corresponding firmware, printer.cfg, specific printed parts, etc.) on our github

:
https://github.com/FYSETC/FYSE TC

-Voron

2 (https://github.com/FYSETC/FYSETC-Voron-2)

Note 1:
All cables have label on, do wiring according to the label shows.

Note 2:
The cable with the labels below are on extruder cable harness TH0, CT, PROBE, HEF, PCF, HE0, E, 24V, GND
Note 3:
USBC cable is optional if you use UART to communicate with Raspi, github :
https://github.com/FYSETC/FYSE TC
SPIDER/blob/main/firmware/Klipp er/Connect%20RPI%20uart.md Note 4:
Check your fan voltage jumpers, all fans in the kit are 24v.
Note 5:
Wango connectors are included in kit, it is useful when you want to add 5V PSU. But we did not use it on this wiring example. Note 6:
The power inlet cord color may different from kit one. Stick to the labels.
Note 7:
Make sure you have appropriate tools, you may be able to rent some equipment from your local hardware store.
Note 8:
Use multimeter to test
connection after you finish wiring. Note 9:
Check the input voltage switch of the power supply. It is located in the highlighted area behind the metal mesh. Make sure the
selection matches your local mains voltage. Recommend to do power supply wiring and test it first before you wire other parts. Note 10:
Make sure the power is off at the breaker before you start and use a voltage tester to verify that. Make sure wires and/or electrical connections are completely dead before you start working on them. Make sure everyone in your home is aware that electrical work is going on. Tape the circuit breaker into the off position.

Z3

Z3

CT

24V

Nevermore Fan

RaspberryPI cable

RaspberryPI cable

PE1

N1

L3

Bed

N

Bed PE(BPE)

USBC

USBC

TH0

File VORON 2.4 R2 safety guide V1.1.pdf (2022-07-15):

V1.1 | Powered by VoronDesign, Produce by FYSETC | www.fysetc.com

# Product Introduction

Thank you for purchasing Voron 3D printer kit from FYSETC. This kit is based on VORON Official 2.4 R2 (no printed parts

included).

In case of any printer-related problem, do not hesitate to contact our customer service. We are glad to receive all of your valuable comments and tips. More product info here: https://github.com/FYSETC/FYSETC-Voron-2

# Product details

Mechanical structure:
- Frame: aluminum box structure
- Printing platform: mic6 thickened aluminum
- Plate: elastic powder steel plate
Print parameters:
- Printing technology: FDM
- Build volume: 250X250X250mm or 300X300X300mm or 350X350X350mm
- Printing layer height: 0.05-0.3mm (use 0.4mm nozzle)
- Maximum printing speed: 200mm/s (recommended: 20-80mm /s)
- Filament diameter: 1.75mm
- Nozzle diameter: 0.4mm
- Filament types: PLA, PETG, PLA-CF carbon fiber, ABS, TPU, HIPS, WOOD, etc. (The default printing

parameter is for PLA, and other filaments should be adjusted according to the parameters provided by the filament supplier.)
Temperature:
- Maximum extruder temperature: 260°C (higher if metal heat break used)
- Maximum temperature of hot bed: 120°C

Software parameters:
- Firmware: Klipper
- Supported formats: STL, G-code, AMF, OBJ
- Input mode: Ethernet, WiFi
- Operating software: Simplify3d, PrusaSlicer, Cura, Repeater host
- Operating system: Windows 7/ Mac OS / Linux Hardware parameters:
- WiFi: support (Based on Raspberry Pi)
- Controller : Spider（TMC2209）+ Raspberry Pi 3/4
- Display: Mini 12864 RGB
- Power supply: Meanwell LRS-200-24
- Input: 100-120V,4.0A / 200-240V, 2.0A
Size & weight:
- Machine size: 522x613x620mm
- Package size: 572x537x337mm （560x525x115mm+560x525x180mm）
- Net weight of machine: 28kg

# Disclaimer

Failure to read the assembly descriptions may lead to personal injury, inferior results, or damage to the 3D printer. Always ensure that anyone who operates the 3D printer

knows and understands the operation description. We cannot control the conditions in which you assemble the kit. For this, and other reasons, we do not assume

responsibility, and expressly disclaim liability for loss, injuries, damage, or expense arising out of, or in any way connected with, the assembly, handling, storage, use or disposal of the product. The information in this handbook is provided without any warranty, expressed or implied, regarding its correctness. Licenses

VORON 2.4 R2 printer is a part of the VoronDesign project, the first open-source 3D printer project free to use under a

GNU | General | Public | License | v3.0 | license
(www.gnu.org/licenses/gpl-3.0.en.html). Permissions: Commercial use, Modification, Distribution, Patent use, Private use

Limitations: Liability, Warranty

You can download the print parts at https://github.com/VoronDesign/Voron-2/tree/V2.4r2/STLs

or purchase our CNC parts at https://www.aliexpress.com/item/10050022 (https://www.aliexpress.com/item/1005002212789450.html) 12789450.html

Follow the manual below to assemble the kit. https://github.com/VoronDesign/Voron-2/tre

e/V2.4r2/Manual

V1.1 | Powered by VoronDesign, Produce by FYSETC | www.fysetc.com

# Safety Guide

Read and understand the assembly manual and safety instructions before beginning to assemble and use the kit. Failure to do so may result in serious injury or death. Save this document. Please be very cautious during any interaction with the

printer. This printer is an electrical device with moving parts and hot-temperature areas. Assembly

- Never disassemble the printer's power supply: it does not contain any parts that can be - repaired by unskilled workers. All repairs must be carried out by qualified technicians. ● In the process of assembling and using the printer, please be careful not to touch or go deep into the

moving position to avoid scratching or pinching. ● Adult supervision required: Prevent children from

touching printer parts or printers unattended, even if the printer is not assembled or printed. Observe children closely and intervene if necessary to prevent potential safety issues and ensure proper use of the printer. Ensure that young children cannot touch small 3D printed parts or 3D printed parts. These are potential suffocation hazards for young children. Wiring

- Before starting the wiring, please read the wiring diagram carefully, understand the installation method of each position, confirm the positive and negative positions, especially confirm that the AC wiring of the PSU is correct and there is no short circuit. The inspection is to observe the wiring position instead of just looking at the color. ● Please make sure that all electronic wires are not

damaged mechanically or otherwise. If so, please stop using the damaged electronic wire immediately and replace it. ● Before powering on for the first time, please make

sure that you have selected the input voltage of the PSU according to your area, otherwise the PSU will be severely burned, or even other peripherals such as the motherboard, and cannot be repaired. Use

- The printer is for indoor use only. Do not expose the printer to rain or snow. Always place the printer in a dry environment and keep at least 30 cm away from other objects. ● Always place the printer in a stable place to prevent it

from falling or tipping over. ● After the machine is debugged, you must be on duty

throughout the printing process to avoid malfunctions. In several cases, it may cause a fire. Please do not leave the printer unattended when the printer is turned on!

- When you unplug the power cord from the socket, pull the plug instead of the power cord to reduce the

risk of damaging the plug or AC power outlet. ● During the process of setting up and operating the

printer, the printing platform and the printing nozzle are at a high temperature. Avoid direct contact with these areas. The nozzle temperature is 190-260°C (374-500°F); the heating bed temperature can reach above 100 °C (212 °F). Temperatures higher than 40 °C (104 °F) can cause harm to the human body. ● The plastic melts during the printing process and

produces a peculiar smell. Put the printer in a well-ventilated place. Manual:

https://github.com/VoronDesign/Voron- 0/raw/Voron0.1/Manuals/Assembly_Man

ual_0.1.pdf

CNC Parts Buy Link:
https://www.aliexpress.com/item/10050 02212789450.html

Print Parts Link:
https://www.thingiverse.com/thing:49141 52

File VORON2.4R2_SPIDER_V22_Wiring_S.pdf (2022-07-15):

### USE FYSETC TMC 2209 V3.1

### USE 4988 or 4988like driver

### USE FYSETC TMC5160/5161/2130 MOSI SCKCS MISO

(SPI4 used for TMC diver SPI,CS and PDN share pins)

V-MOTOR(24V) GND

# A2A1B1B2VIO(3.3V) GND

ENABLE
(not used)MS1
(not used)MS2
TX
(not used)RX
(not used)CLK

# STEP DIR PDN DIAG

PDN: It is connected to TX for communication between TMC and MCU, using single wire. The

jumper cap shown in the figure must be setted before the drive module install. DIAG: It is used to go home without sensing, while ensuring that the jumper corresponding to the limit is in the closed state. ¹x Jumper cap

4x Jumper cap

4x Jumper cap GND

DIN

+5V | USB Pins Out: used to connect the Raspberry Pi inside the printer via USB. | The type-C USB socket is used by default,

and type-A is also reserved. If you need it, you can Add it by yourself. SD Pins Out: You can use the SD Card in a farther position by the SD module, but it is not recommended to exceed 30cm.

V-MOTOR(24V) GND

# A2A1B1B2VIO(3.3V) GND

# ENABLE MOSI SCKCS MISO

(not used)CLK

# STEP DIR DIAG

DIAG: It is used to go home without sensing, while ensuring that the jumper corresponding to the limit is in the closed state. V-MOTOR(24V) GND

# A2A1B1B2VIO(3.3V) GND

# ENABLE MS1 MS2 MS3 RST

SLEEP
STEP DIR
LCD | SD

The markings of EXP1 and EXP2 may be different from those of some displays. If it cannot be displayed normally, please try to reverse EXP1 and EXP2 if the program is correct.

Install this jumper
cap(pin1&pin2) to use internal DC5V,close the other two(pin2&pin3) to

use USB5V(recommend
only for debug).

# HOT SURFACE DO NOT TOUCH

# AC Heating Bed 110/220V INPUT

VIN

5V | SLEEP MS3 MS2 MS1
PB14 | PA0 PA1 | PA2 | PA3

3
2
1

The spider provides a serial port for connecting to the Raspberry Pi or WiFi module, and this interface has a strong enough (8A MAX) 5V power supply. In order to use the only hardware serial port of the Raspberry Pi, you need to disable the console function and map the hardware serial port to GPIO14 and GPIO15. You can refer here: sudo raspi-config

=> Interfacing Option
=> Serial => NO

=> YES
sudo nano /boot/config.txt => add this line : dtoverlay=pi3-disable-bt => then

sudo reboot sudo nano /boot/cmdline.txt

=> remove the word phase "console=serial0,115200" or "console=ttyAMA0,115200"

sudo reboot PA⁹/RX¹ PA¹⁰/TX¹

PC0 | PC1 | PC2 | PC3

Jumper Cap Set： PL08N=VIN

Bltouch=5V

E

Z2

### Rear-Right

# Exhaust Fan

6020 FAN 24V

PB1 PB0

48V Driver Support（M1 & M2）: 1.If you use 24V, you need to connect the 24V-PIN

and 48V-PIN, and use the jumper plug that we provide.

2.If you use 48V, you need to connect an external power supply to the 48-PIN and GND-PIN using the
connecting wires provided by us. PA13 | PA14 | PB2 | PB13

X/Y

# Endstop Z Endstop

# 25A SSR

# Notice： Please select the voltage of

# your area before powering

up.

Please make sure that your heating bed is in line with the voltage of your country or region. The high voltage version will heat very slowly when used at low voltage and may not reach the target temperature. The low-voltage version is used in the high-voltage version to heat up quickly, even exceeding the temperature you

set, which is very dangerous.

Nozzle Heating 5A MAX WSD3050

Temperature Sensor NTC/PT100/Thermocouple(Need AD597 add on)

3.3V 4.7K(0.1%)Pull Up

Probe 调平

HE0 加热棒

24V共用 | CT 箱体温度
PCF 打印冷却 | HEF 热端散热
AGND 模拟地 | S2B
TH0 测温 | S2A
GND 共用地 | S1A
XES 预留 | S1B
5V | SERVO

Z1

### Rear-left

E
Z0

### Front-left

B Z3 Front-Right

# Print Cooling Fan

6020 FAN 24V | Hotend Fan 4010 FAN 24V | AfterburnerToolhead PCB x https://github.com/FYSETC/FYSETC- Afterburner_Toolhead_PCB_x

# AfterburnerToolhead PCB x SOCKET

# AfterburnerToolhead PCB x SOCKET Check the wiring at lower left

# To Spider E-MOT socket

# Controller Fan x2

6020 FAN 24V

Nevermore filter 4010 FAN 24V x2 | A

# Spider v2.2 Voron 2.4 R2

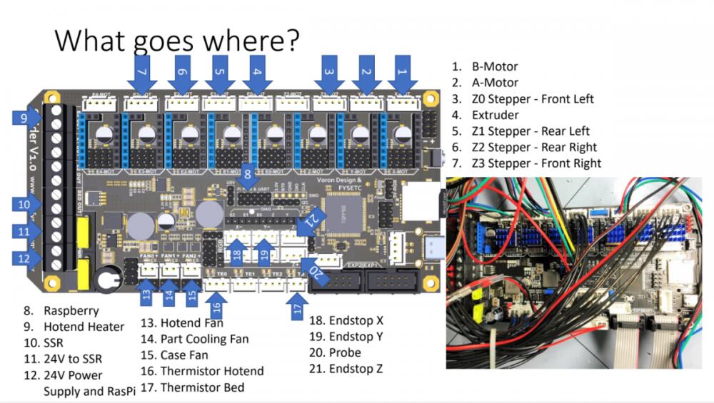
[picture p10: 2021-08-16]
Wiring.jpg

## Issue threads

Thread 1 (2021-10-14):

Kit Issues

InoxDragoon, 2021-10-14:
I believe I got one of the last 1.0 kits, since my belts were too short and I didn't get the tools. So some of these items may have already been addressed.

That said: a few suggestion, if able:

1) Add a paper with this Repository in the kit! I have my printer about 75% built and some of this info would have been really useful before hand.

2) What wires do what in the kit? Some are self explainatory, but others not so much... Namely: Which stepper cables go to what stepper? Which of the 2 connectors on the XY endstop harness goes where? What are some of the loose wires for? which side of the Pi/Spider cable go to which board? With some research and/or trial&error these can be figured out; but a more streamlined assembly could be accomplished if the bags were labeled or a pallet picture was shown here. I think the v2_spider_wiring shows some of this, but the X and Y Endstop wires are shown as all black, were as I have Red/Black/White/Yellow that split off to 2 3 pin connectors with one of them going to pins 1 and 3, and the other conforms to pin 1 and 2.

3) Do not tin mains wiring! this is a fire hazard as high amp draws can cause the solder to melt, then cause electrical arcing in the screw terminals and/or solder the wire into the terminal. either pre-strip the wire a little (leaving the insulation on the end) or use ferrules.

4) A sample layout of the basement would be helpful. i've had to re-order the board/power supply a couple times because some wires were too short for my layout. I started with what was shown on Voron's website and had to move everything around a couple times as I added wires.

5) Link to the Spider Repository or list Klipper configs on this Repository. At the least, provide a printer.cfg on here that corrlates with the info here. I know the newer kit has Klipper pre-flashed, but I'm not sure what's best starting out. would that firmware work for my kit? better yet, if someone wants to try a different firmware, but then revert back to Klipper, they could roll back easier this way. Long story short, a baseline would be helpful.

GerogeFu, 2021-11-11:
Thanks for your feedback here. I update the repo, hope it can help. You suggestions help a lot.

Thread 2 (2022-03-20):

Wrong endstop connectors shown in diagram (Spider 2.2)

cscashby, 2022-03-20:
The diagram for the Spider 2.2 wiring (https://github.com/FYSETC/FYSETC-Voron-2/blob/main/VORON2.4_SPIDER_V22_WIRING.pdf) shows the endstops connected to the X+ and Y+ when it should be X- and Y- - as per the default klipper config (https://github.com/VoronDesign/Voron-2/tree/Voron2.4/firmware/klipper_configurations/Spider linked from the README)

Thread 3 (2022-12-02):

all stl

mrnoobmrnoob, 2022-12-02:
hi i have a kit for a 350mm voron with cnc parts, i have liked if all the parts that need printing for youre kit is in this github. it a bit of a jungle when you look att all the stl's that voron has and you only look for 10 to 20 parts. :)

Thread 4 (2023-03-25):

Make it clearer how to enable sensorless homing

Adrian-at-CrimsonAuzre, 2023-03-25:
I spent an afternoon trying to get sensorless homing to work because I missed the fine print in the corner of the wiring diagram that says to "while ensuring that the jumper corresponding to the limit is in a closed state" and [another reference](https://wiki.fysetc.com/images/Spider_V2.3_Pinout.jpg) that has an unlabeled section showing the diag and limit pins side by site. Can the documentation be updated to _explicitly_ call out these jumpers for sensorless homing?

luisfosoares, 2024-06-05:
@Adrian-at-CrimsonAzure As it was not added yet can you describe the correct way to make sensorless homing?

Thanks

Adrian-at-CrimsonAzure, 2024-06-05:
It's been a while since I set this up, but I believe I bridged the two right most jumper pairs on the "diag" header to enable sensorless endstops for the A and B motors.
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

Then I used [this config](https://github.com/Print3DWorld/Voron2.4-FYSETCSpider/blob/main/sensorless.cfg) and tuned the stall guard threshold to work with my printer. This configuration repo is a _very_ good starting point for setting up your Voron in general.

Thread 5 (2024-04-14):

BOM does not state type of powerinlet

Altirix, 2024-04-14:
Theres two STL versions for IEC

power_inlet_IECGS_1mm

and

power_inlet_IECGS_1.2mm

the kit seems to ship with power_inlet_IECGS_1.2mm

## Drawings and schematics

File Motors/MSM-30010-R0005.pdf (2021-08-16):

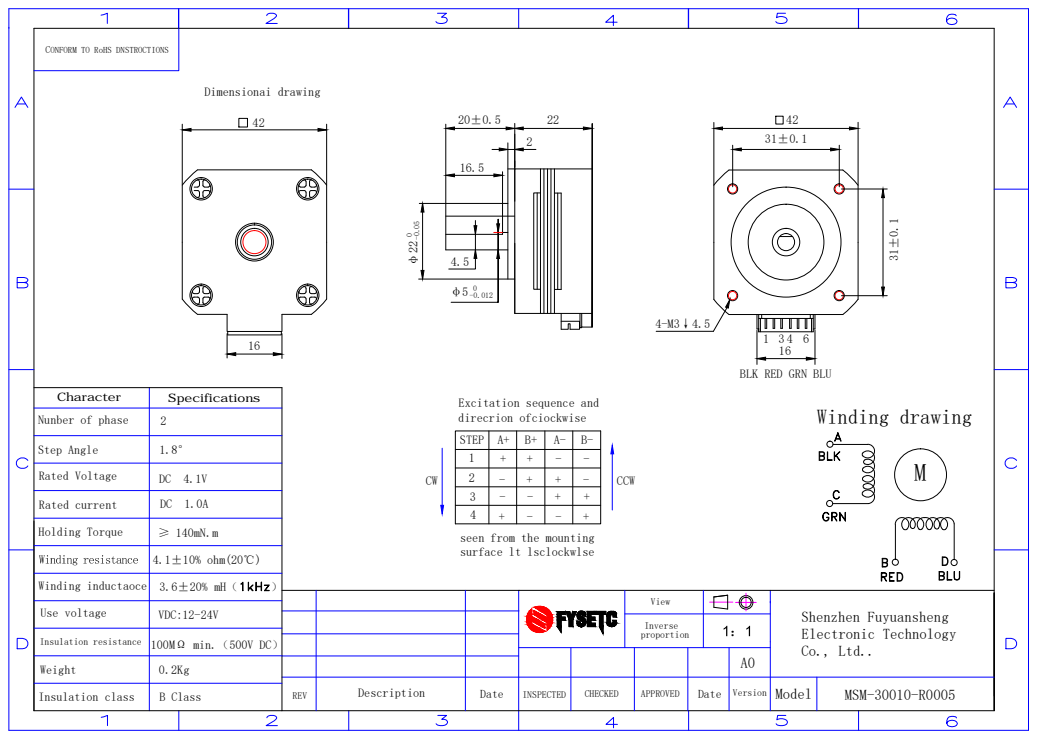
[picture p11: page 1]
Winding drawing M

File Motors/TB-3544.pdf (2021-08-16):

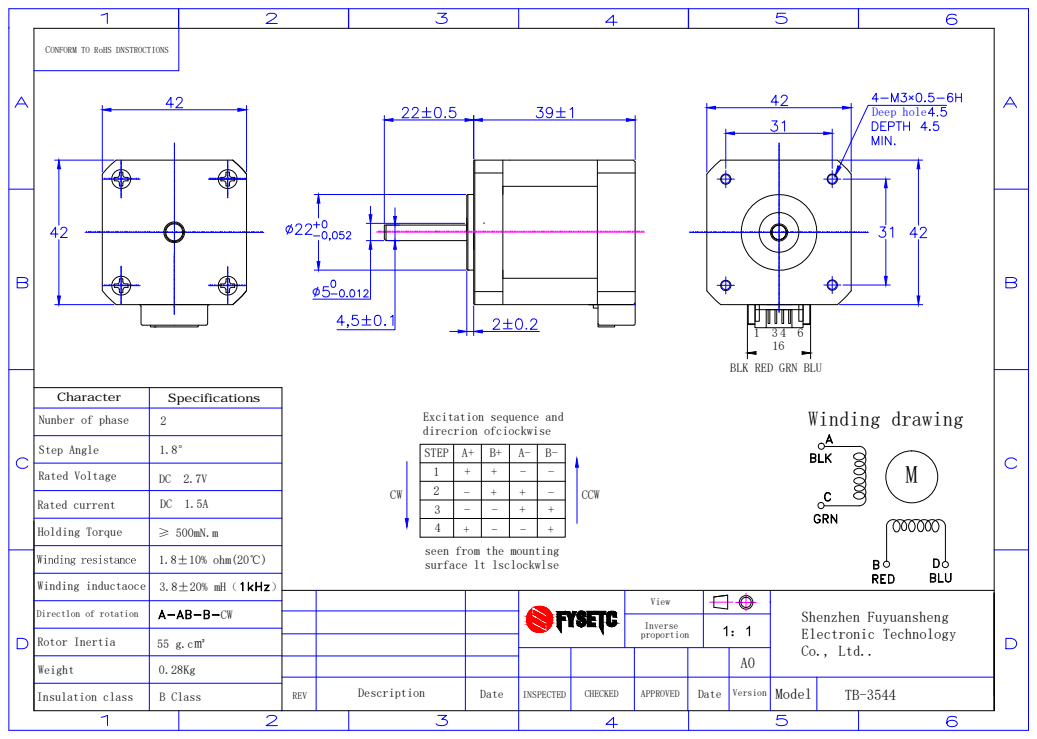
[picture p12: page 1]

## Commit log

2021-06-05 Upload information
    Upload information
    [Back_Panel_250.DXF, Back_Panel_300.DXF, Back_Panel_350.DXF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]
2021-06-25 Update klipper_configurations
    [Voron2_SKR_13_Config.cfg, Voron2_SKR_14_Config.cfg]
2021-06-25 Renamed VORON-2
    [Back_Panel_250.DXF, Back_Panel_300.DXF, Back_Panel_350.DXF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]
2021-07-22 Update file location
    Update file location
    [Back_Panel_250.DXF, Back_Panel_300.DXF, Back_Panel_350.DXF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]
2021-08-16 Update kit Spider wiring
2021-08-16 Add Spider Mount stl information
2021-09-08 Rename 'Package list.md' to 'BOM.md' and rearrange items form
2021-09-08 Add revsion v1.1 BOM
2021-09-14 New z chain mount
    [Z_Chain_Lower_Mount.STL, Z_Chain_Upper_Mount.STL]
2021-09-25 Add thermal fuse parameter
2021-10-28 Change stepper motor name to SKU
2021-10-29 Remove Thingiverse printed part link
2021-11-10 Add motors cable length parameter
2021-11-11 Add printer.cfg link and xy endstop wiring
2021-11-22 Add VORON wiring diagram
    Add VORON wiring diagram
2021-12-01 Upload Spider v2.2 wiring
2021-12-01 Rename wiring file name
2022-03-02 Update wiring
2022-03-22 UpdateBOM
    Update BOM
2022-05-30 Upload R2 wiring
2022-08-29 update readme
    update PCB Cover
2022-08-30 Update BOM.md
    Update BOM error
2022-12-21 Upload Spider v23 wiring
2023-08-22 Upload the spider 3.0 wiring diagram
    Upload the spider 3.0 wiring diagram
